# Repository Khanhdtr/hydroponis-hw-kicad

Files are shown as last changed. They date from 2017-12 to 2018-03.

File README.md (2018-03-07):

# Hydroponics hardware
Mạch thủy canh thông minh
## Yêu cầu thiết kế
-Nguồn vào 12V DC dùng LM2596 => 5V
- IC dùng module Maple Mini + NodeCMU
- Đọc các giá trị cảm biến DS18b20, Dht11, EC, Bh1750 , water level
- Sử dụng Touchpad key 2x4 để tương tác
- Sử dụng LCD16x2 để hiển thị các thông số cảm biến và trạng thái
- Tương tác với người dùng thông qua giao App Blynk
## Tổng quan
### Sơ đồ nguyên lý
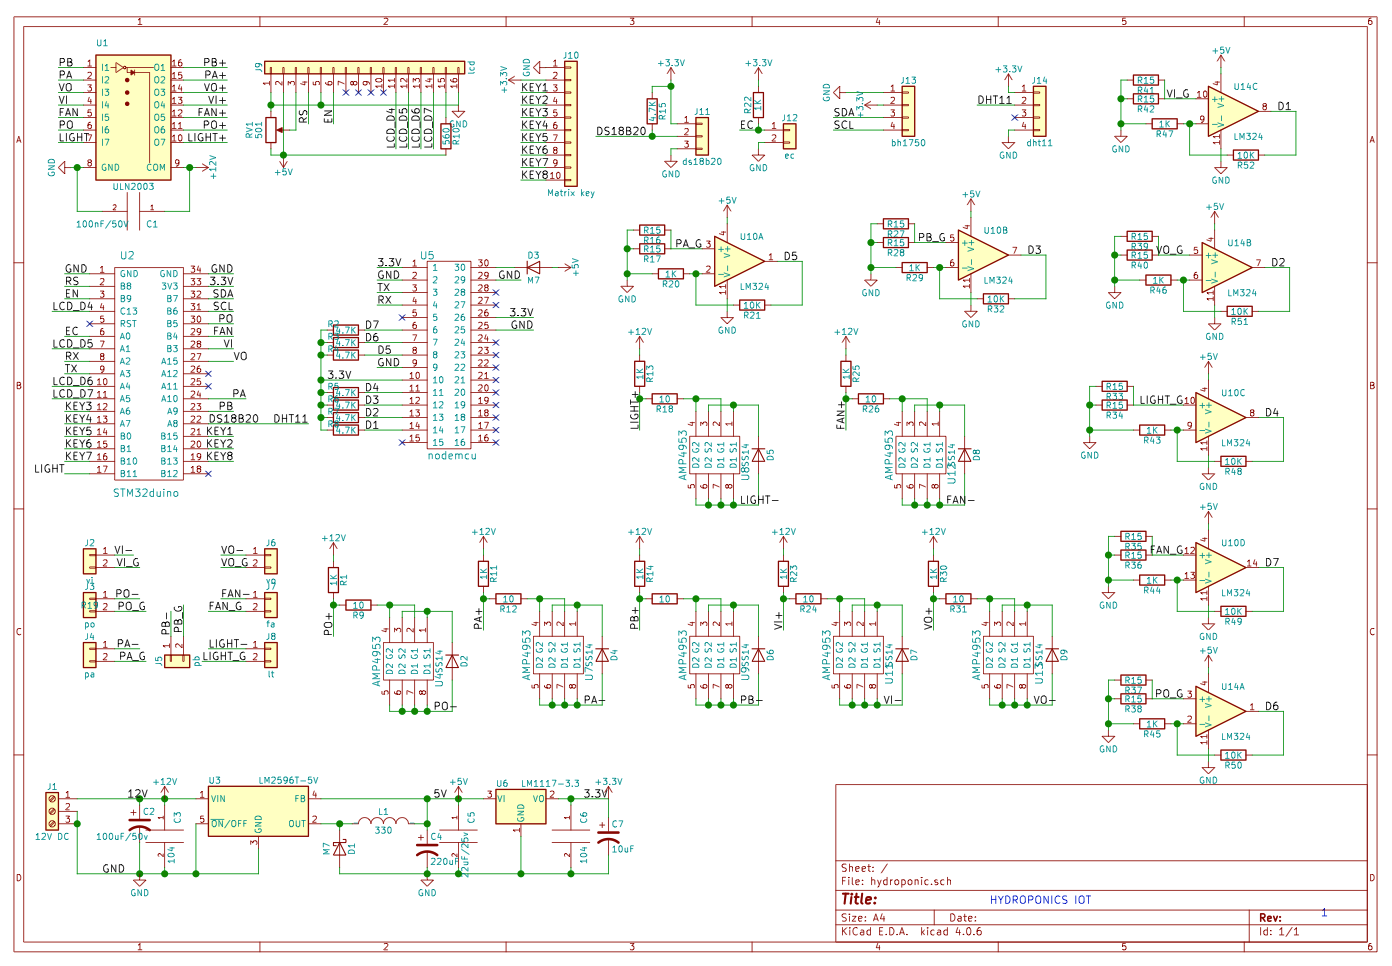
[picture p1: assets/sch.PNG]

### PCB
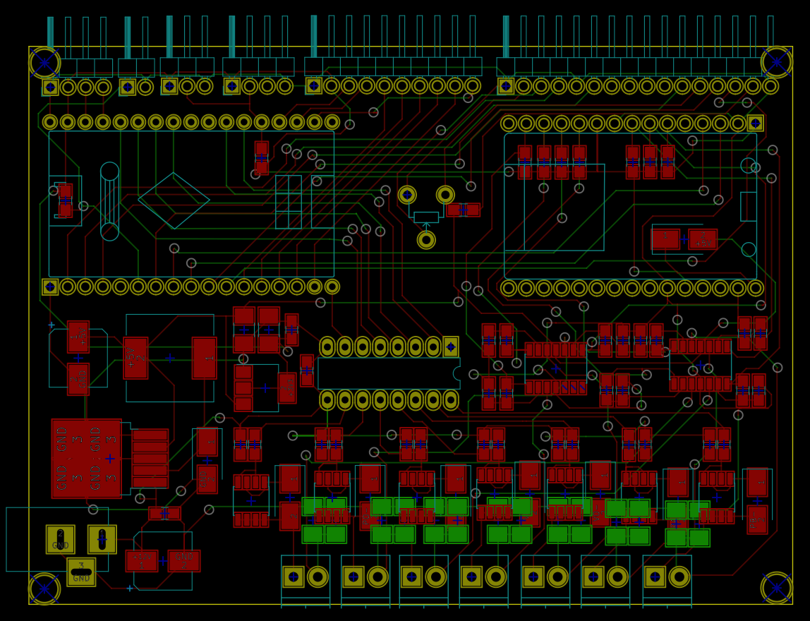
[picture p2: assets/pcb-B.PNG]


### 3D
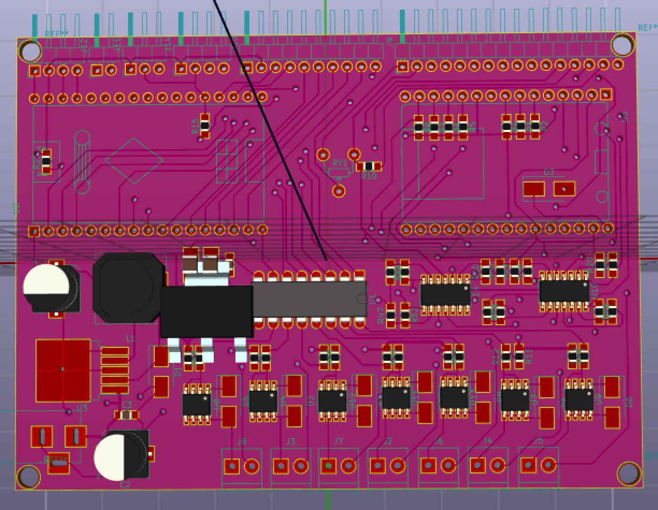
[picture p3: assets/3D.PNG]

### TOP
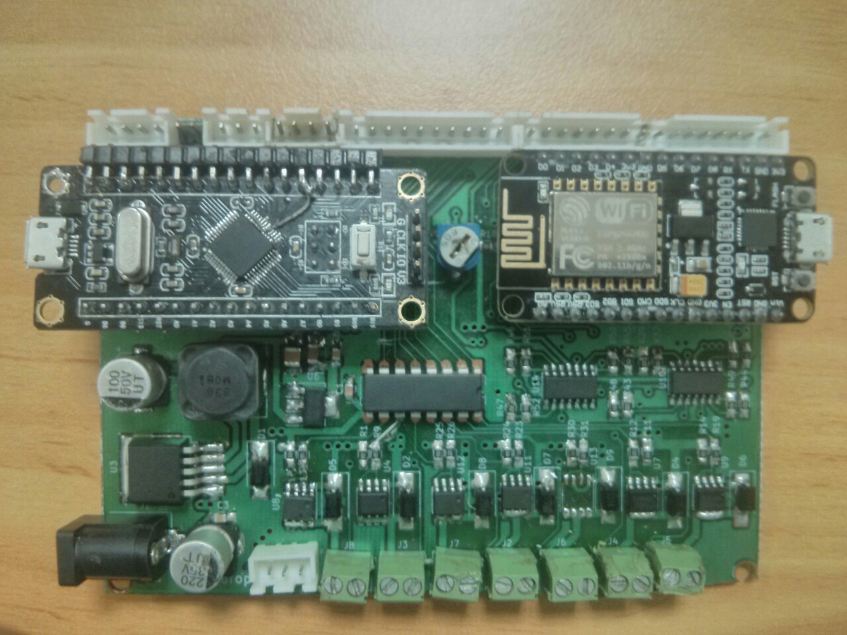
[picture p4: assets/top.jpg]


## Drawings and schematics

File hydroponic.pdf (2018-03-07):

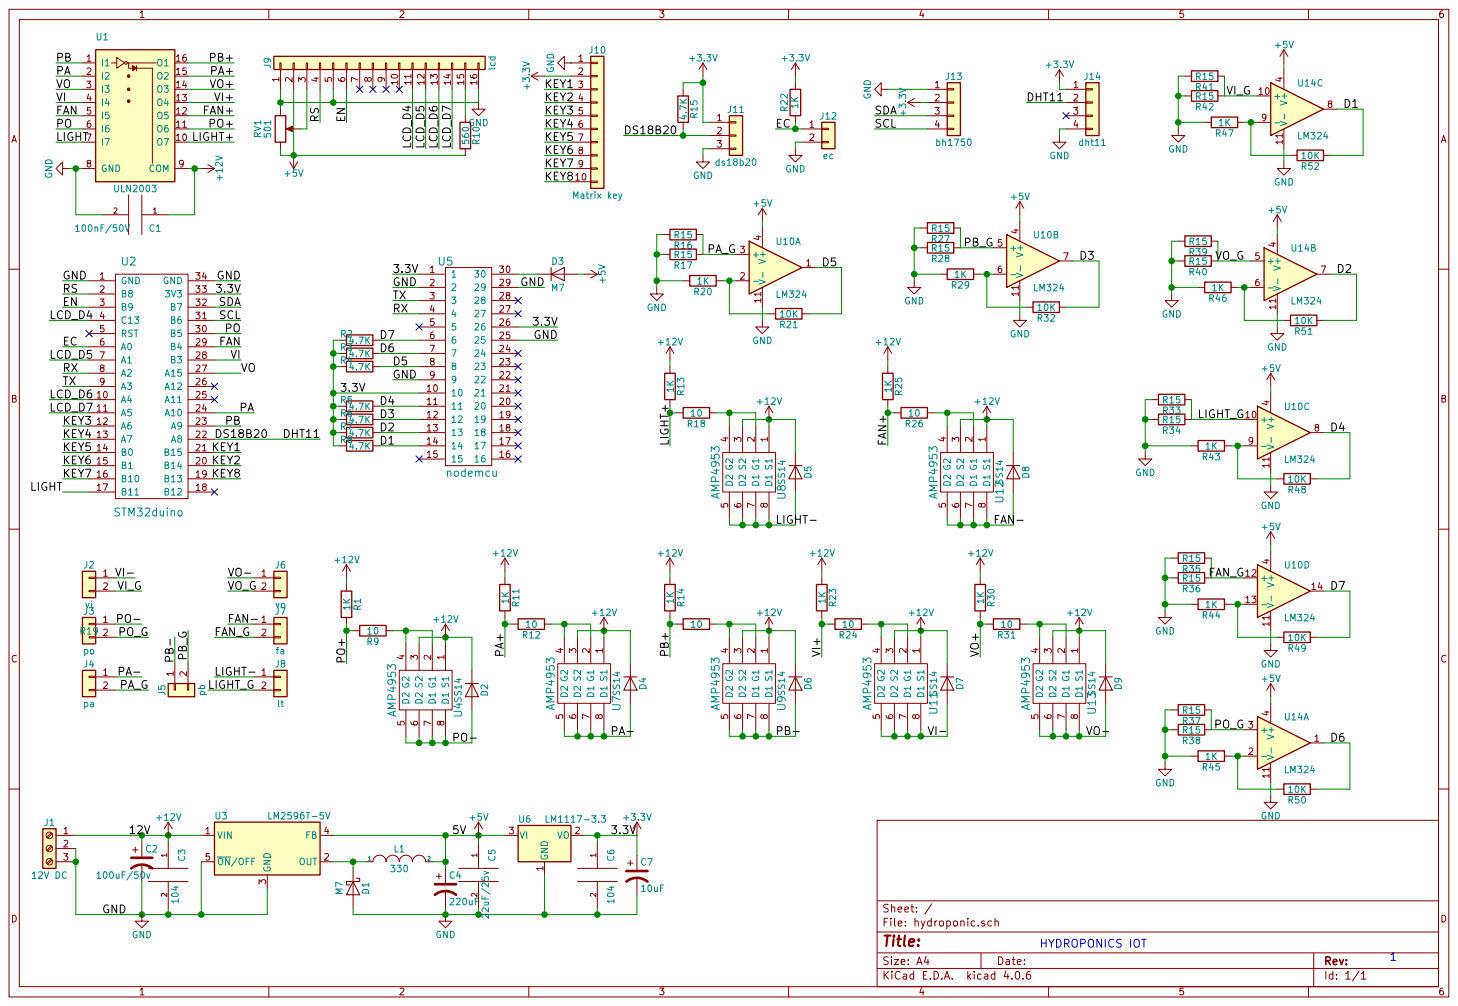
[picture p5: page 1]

10 +12V PO+ PA+ PB+ FAN+

10

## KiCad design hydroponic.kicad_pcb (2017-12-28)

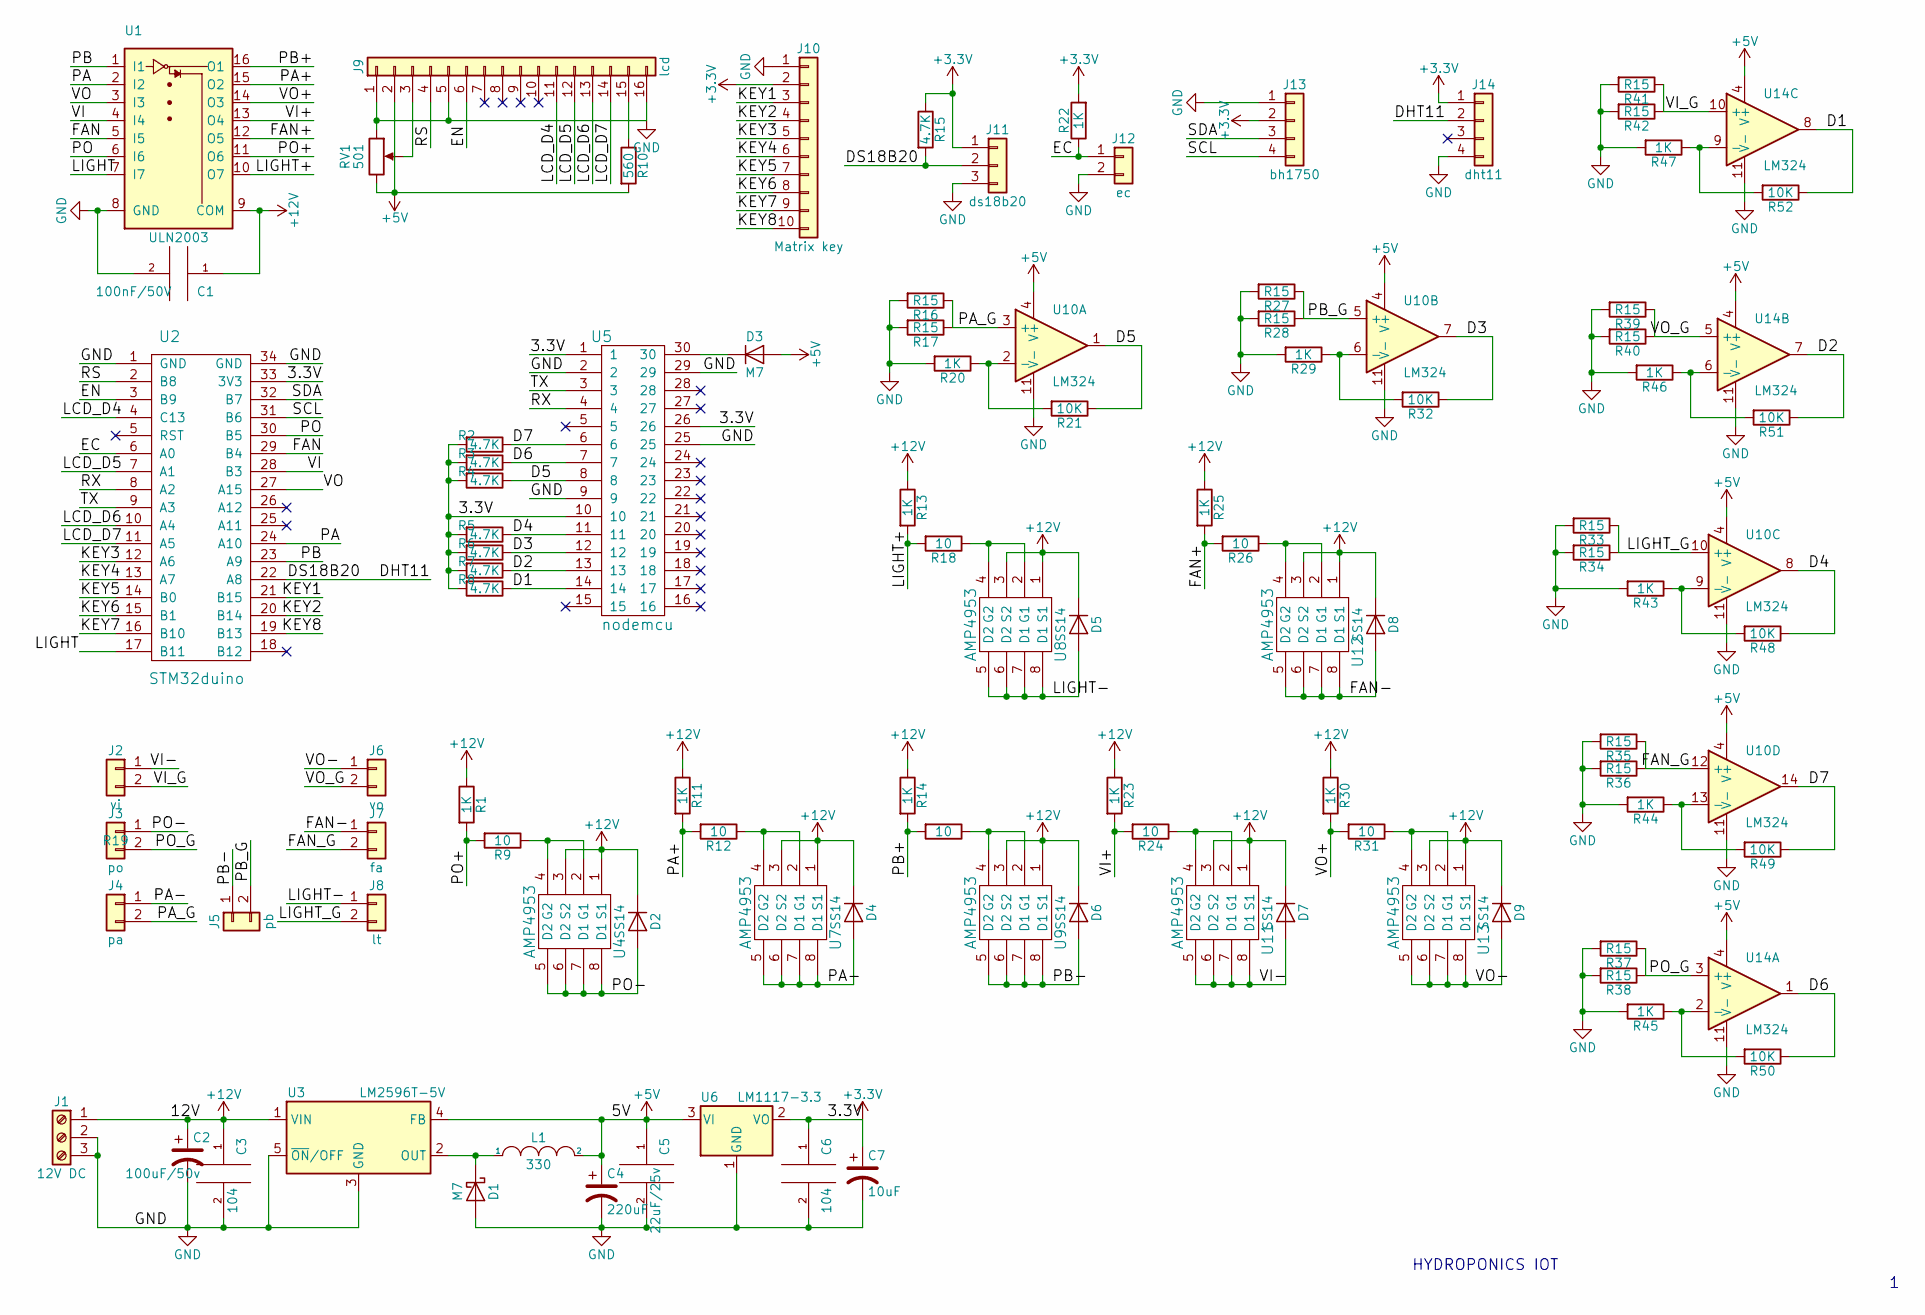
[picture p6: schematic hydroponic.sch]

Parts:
C1: 100nF/50V; C_0805_HandSoldering
C2: 100uF/50v; CP_Elec_8x10
C3, C6: 104; C_0805_HandSoldering
C4: 220uF; CP_Elec_8x10
C5: 22uF/25v; C_1210_HandSoldering
C7: 10uF; C_1210_HandSoldering
D1, D3: M7; D_SMB_Handsoldering
D2, D4, D5, D6, D7, D8, D9: SS14; D_SMB_Handsoldering
J1: 12V DC; BARREL_JACK
J2: vi; TerminalBlock_Phoenix_PT-3.5mm_2pol
J3: po; TerminalBlock_Phoenix_PT-3.5mm_2pol
J4: pa; TerminalBlock_Phoenix_PT-3.5mm_2pol
J5: pb; TerminalBlock_Phoenix_PT-3.5mm_2pol
J6: vo; TerminalBlock_Phoenix_PT-3.5mm_2pol
J7: fa; TerminalBlock_Phoenix_PT-3.5mm_2pol
J8: lt; TerminalBlock_Phoenix_PT-3.5mm_2pol
J9: lcd; Pin_Header_Angled_1x16_Pitch2.54mm
J10: Matrix key; Pin_Header_Angled_1x10_Pitch2.54mm
J11: ds18b20; Pin_Header_Angled_1x03_Pitch2.54mm
J12: ec; Pin_Header_Angled_1x02_Pitch2.54mm
J13: bh1750; Pin_Header_Angled_1x04_Pitch2.54mm
J14: dht11; Pin_Header_Angled_1x04_Pitch2.54mm
L1: 330; L_12x12mm_h4.5mm
R1, R11, R13, R14, R20, R22, R23, R25, R29, R30, R43, R44, R45, R46, R47: 1K; R_0805_HandSoldering
R2, R3, R4, R5, R6, R7, R8, R15: 4.7K; R_0805_HandSoldering
R9, R12, R18, R19, R24, R26, R31: 10; R_0805_HandSoldering
R10: 560; R_0805_HandSoldering
R16, R17, R27, R28, R33, R34, R35, R36, R37, R38, R39, R40, R41, R42: R15; R_1210_HandSoldering
R21, R32, R48, R49, R50, R51, R52: 10K; R_0805_HandSoldering
RV1: 501; VARmini
U1: ULN2003; DIP-16_W7.62mm_LongPads
U2: STM32duino; MapleMini
U3: LM2596T-5V; TO-263-5_TabPin3
U4, U7, U8, U9, U11, U12, U13: AMP4953; SOIC-8_3.9x4.9mm_Pitch1.27mm
U5: nodemcu; NodeMCU
U6: LM1117-3.3; SOT-223-3_TabPin2
U10, U14: LM324; SOIC-14_3.9x8.7mm_Pitch1.27mm

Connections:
+3V3: C6.1, C7.1, J10.2, J11.1, J13.2, J14.1, R2.2, R3.2, R4.2, R5.2, R6.2, R7.2, R8.2, R15.1, R22.2, U2.33 (3V3), U5.1, U5.10, U5.26, U6.2 (VO)
+5V: C4.1, C5.1, D3.2 (A), J9.2, L1.2, R10.2, RV1.3, U3.4 (FB), U6.3 (VI), U10.4 (V+), U14.4 (V+)
+12V: C1.1, C2.1, C3.1, D2.1 (K), D4.1 (K), D5.1 (K), D6.1 (K), D7.1 (K), D8.1 (K), D9.1 (K), J1.1, R1.1, R11.1, R13.1, R14.1, R23.1, R25.1, R30.1, U1.9 (COM), U3.1 (VIN), U4.1 (S1), U4.3 (S2), U7.1 (S1), U7.3 (S2), U8.1 (S1), U8.3 (S2), U9.1 (S1), U9.3 (S2), U11.1 (S1), U11.3 (S2), U12.1 (S1), U12.3 (S2), U13.1 (S1), U13.3 (S2)
/D1: R8.1, R52.1, U5.14, U14.8
/D2: R7.1, R51.1, U5.13, U14.7
/D3: R6.1, R32.1, U5.12, U10.7
/D4: R5.1, R48.1, U5.11, U10.8
/D5: R4.1, R21.1, U5.8, U10.1
/D6: R3.1, R50.1, U5.7, U14.1
/D7: R2.1, R49.1, U5.6, U10.14
/DHT11: J11.2, J14.2, R15.2, U2.22 (A8)
/EC: J12.1, R22.1, U2.6 (A0)
/EN: J9.6, U2.3 (B9)
/FAN: U1.5 (I5), U2.29 (B4)
/FAN+: R25.2, R26.2, U1.12 (O5)
/FAN-: D8.2 (A), J7.1, U12.5 (D2), U12.6 (D2), U12.7 (D1), U12.8 (D1)
/FAN_G: J7.2, R35.1, R36.1, U10.12 (+)
/KEY1: J10.3, U2.21 (B15)
/KEY2: J10.4, U2.20 (B14)
/KEY3: J10.5, U2.12 (A6)
/KEY4: J10.6, U2.13 (A7)
/KEY5: J10.7, U2.14 (B0)
/KEY6: J10.8, U2.15 (B1)
/KEY7: J10.9, U2.16 (B10)
/KEY8: J10.10, U2.19 (B13)
/LCD_D4: J9.11, U2.4 (C13)
/LCD_D5: J9.12, U2.7 (A1)
/LCD_D6: J9.13, U2.10 (A4)
/LCD_D7: J9.14, U2.11 (A5)
/LIGHT: U1.7 (I7), U2.17 (B11)
/LIGHT+: R13.2, R18.2, U1.10 (O7)
/LIGHT-: D5.2 (A), J8.1, U8.5 (D2), U8.6 (D2), U8.7 (D1), U8.8 (D1)
/LIGHT_G: J8.2, R33.1, R34.1, U10.10 (+)
/PA: U1.2 (I2), U2.24 (A10)
/PA+: R11.2, R12.2, U1.15 (O2)
/PA-: D4.2 (A), J4.1, U7.5 (D2), U7.6 (D2), U7.7 (D1), U7.8 (D1)
/PA_G: J4.2, R16.1, R17.1, U10.3 (+)
/PB: U1.1 (I1), U2.23 (A9)
/PB+: R14.2, R19.2, U1.16 (O1)
/PB-: D6.2 (A), J5.1, U9.5 (D2), U9.6 (D2), U9.7 (D1), U9.8 (D1)
/PB_G: J5.2, R27.1, R28.1, U10.5 (+)
/PO: U1.6 (I6), U2.30 (B5)
/PO+: R1.2, R9.2, U1.11 (O6)
/PO-: D2.2 (A), J3.1, U4.5 (D2), U4.6 (D2), U4.7 (D1), U4.8 (D1)
/PO_G: J3.2, R37.1, R38.1, U14.3 (+)
/RS: J9.4, U2.2 (B8)
/RX: U2.8 (A2), U5.4
/SCL: J13.4, U2.31 (B6)
/SDA: J13.3, U2.32 (B7)
/TX: U2.9 (A3), U5.3
/VI: U1.4 (I4), U2.28 (B3)
/VI+: R23.2, R24.2, U1.13 (O4)
/VI-: D7.2 (A), J2.1, U11.5 (D2), U11.6 (D2), U11.7 (D1), U11.8 (D1)
/VI_G: J2.2, R41.1, R42.1, U14.10 (+)
/VO: U1.3 (I3), U2.27 (A15)
/VO+: R30.2, R31.2, U1.14 (O3)
/VO-: D9.2 (A), J6.1, U13.5 (D2), U13.6 (D2), U13.7 (D1), U13.8 (D1)
/VO_G: J6.2, R39.1, R40.1, U14.5 (+)
GND: C1.2, C2.2, C3.2, C4.2, C5.2, C6.2, C7.2, D1.2 (A), J1.2, J1.3, J9.1, J9.5, J9.16, J10.1, J11.3, J12.2, J13.1, J14.4, R16.2, R17.2, R20.2, R27.2, R28.2, R29.2, R33.2, R34.2, R35.2, R36.2, R37.2, R38.2, R39.2, R40.2, R41.2, R42.2, R43.2, R44.2, R45.2, R46.2, R47.2, RV1.1, U1.8 (GND), U2.1 (GND), U2.34 (GND), U3.3 (GND), U3.5 (~ON~/OFF), U5.2, U5.9, U5.25, U5.29, U6.1 (GND), U10.11 (V-), U14.11 (V-)
unnamed: D1.1 (K), L1.1, U3.2 (OUT)
unnamed: D3.1 (K), U5.30
unnamed: J9.3, RV1.2
unnamed: J9.15, R10.1
unnamed: R9.1, U4.2 (G1), U4.4 (G2)
unnamed: R12.1, U7.2 (G1), U7.4 (G2)
unnamed: R18.1, U8.2 (G1), U8.4 (G2)
unnamed: R19.1, U9.2 (G1), U9.4 (G2)
unnamed: R20.1, R21.2, U10.2 (-)
unnamed: R24.1, U11.2 (G1), U11.4 (G2)
unnamed: R26.1, U12.2 (G1), U12.4 (G2)
unnamed: R29.1, R32.2, U10.6 (-)
unnamed: R31.1, U13.2 (G1), U13.4 (G2)
unnamed: R43.1, R48.2, U10.9 (-)
unnamed: R44.1, R49.2, U10.13 (-)
unnamed: R45.1, R50.2, U14.2 (-)
unnamed: R46.1, R51.2, U14.6 (-)
unnamed: R47.1, R52.2, U14.9 (-)

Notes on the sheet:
HYDROPONICS IOT

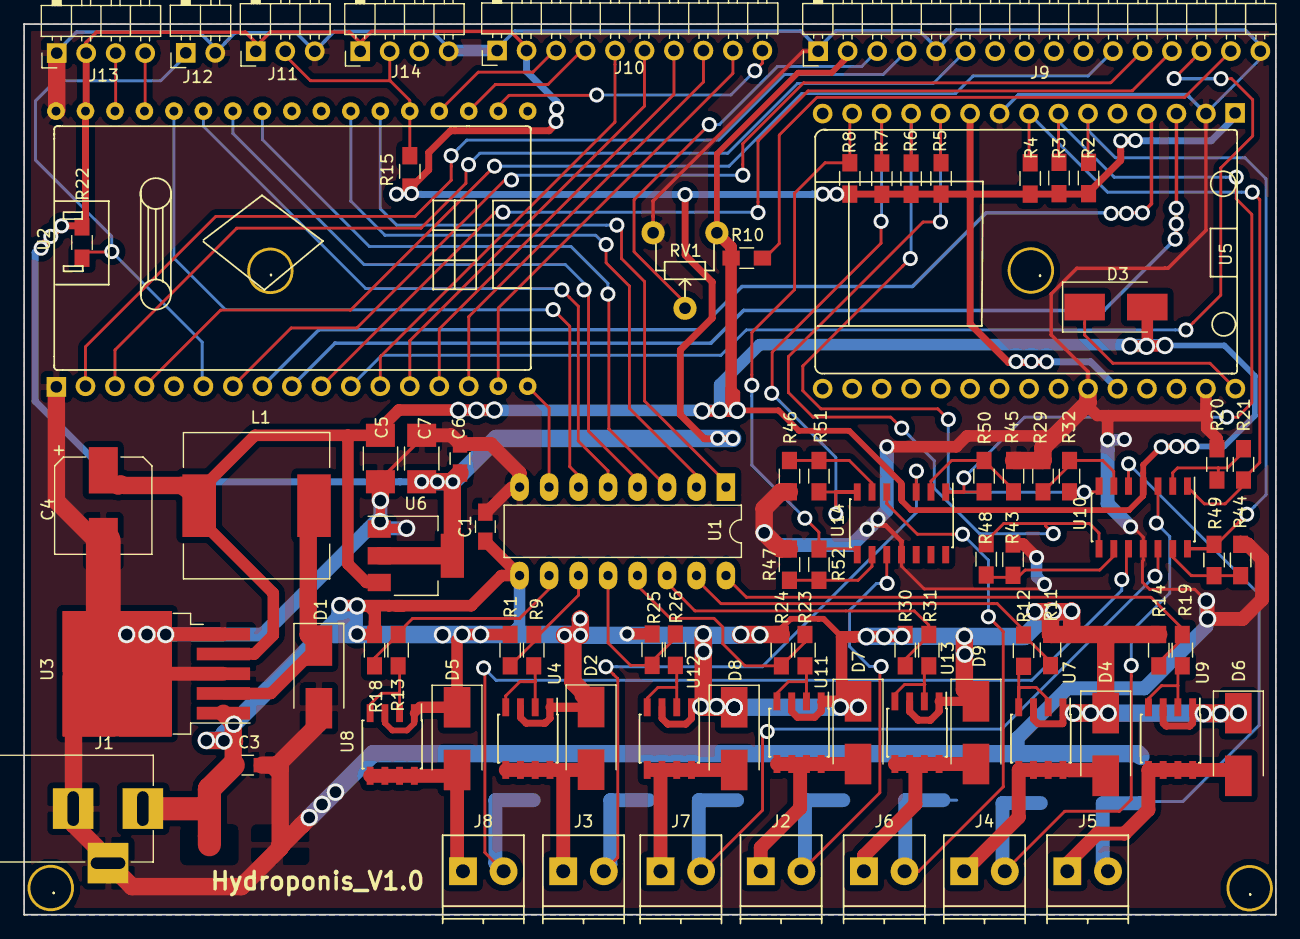
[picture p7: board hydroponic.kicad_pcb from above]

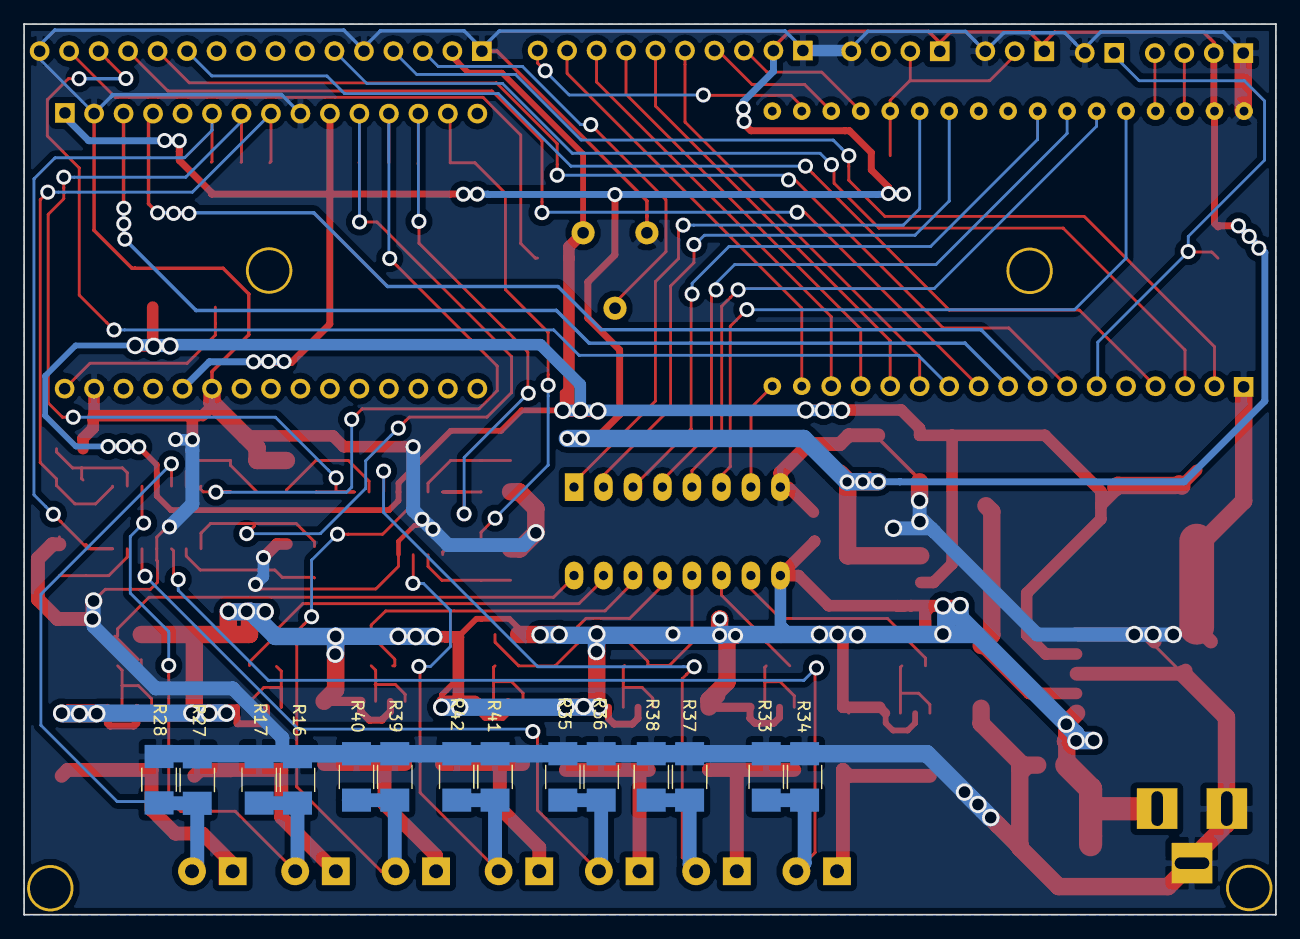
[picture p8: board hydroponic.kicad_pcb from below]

Board: 2 copper layers, 107.8 x 76.7 mm, 101 parts (14 on the bottom side), 77 nets.

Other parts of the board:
., .#2, .#3, .#4: Drill_3.5mm

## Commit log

2017-12-27 initial hydroponics hardware
    [hydroponic.kicad_pcb, hydroponic.sch]
2017-12-28 add net 12v to AMP4953
    [hydroponic.kicad_pcb, hydroponic.sch]
2017-12-28 edit all power in pcb
    [hydroponic.kicad_pcb]
2017-12-28 edit all net in pcb
    [hydroponic.kicad_pcb]
2017-12-28 add gerber file
    [hydroponic-B.Cu.gbr, hydroponic-B.Mask.gbr, hydroponic-B.SilkS.gbr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]
